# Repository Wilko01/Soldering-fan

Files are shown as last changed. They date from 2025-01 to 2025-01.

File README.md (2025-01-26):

# Soldering fume extractor

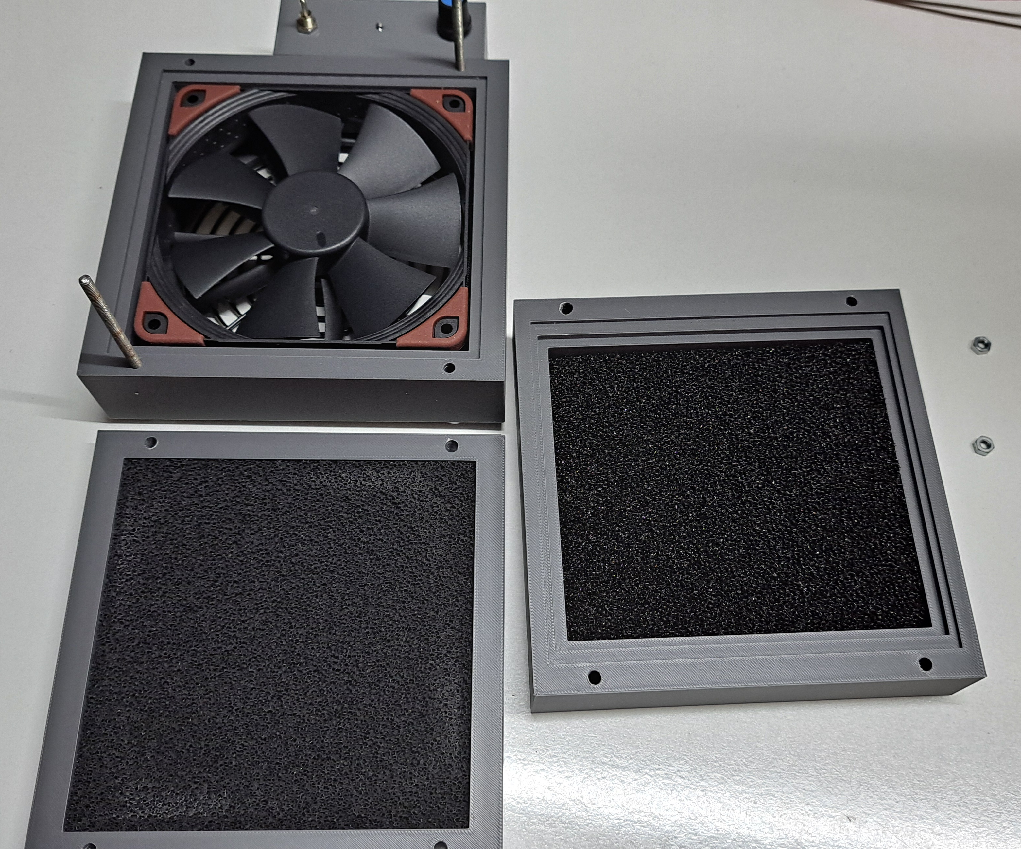
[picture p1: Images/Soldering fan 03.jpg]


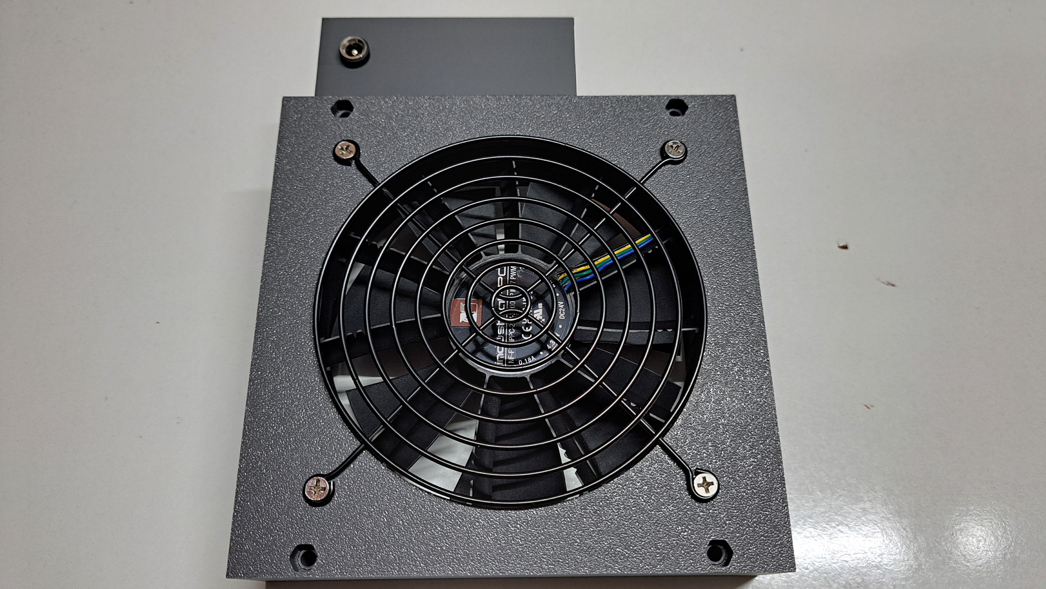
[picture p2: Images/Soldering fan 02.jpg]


## Description and operation instructions
Fumes which might be hazzourdus may be released during soldering. I therefor created a modular fume suction box. It can be used with active carbon, Hepa or any other filters.
The fan can be controlled via a potentiometer. Use a 24V, 2A power adapter. Turn the fan on via the switch. A green LED will turn on.

 ## Technical description
A 120mm 24V PC fan is used where the RPM is controlled via the PWM signal. A 555 generates the PWM signal. The PWM signal may not exceed 5V as it will damage the fan. The tacho of the fan is not used.
A more filters to the box, but keep in mind that by every filter the suction of the air will be reduced. The 555 will generate a 1kHz signal. This is not optimal as Noctua describes to use a 25kHz signal, but works fine.

PWM info: https://circuitdigest.com/fullimage?i=circuitdiagram/PWM-generation-using-555-timer-IC-circuit-diagram.png

### Parts
1 x Noctua NF-F12 industrialPPC-24V-3000 SP IP67
PLA filament
3 x 2-12mm screw
2 x 2,6-8mmm srew
4 x 85mm M4 bolt
4 x M4 cnut
Some wires

1 x 24V PWM fan

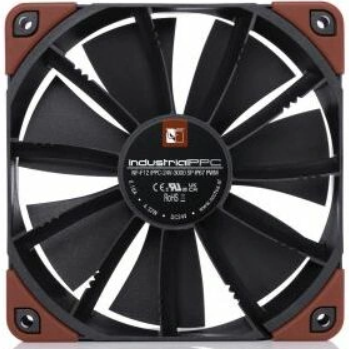
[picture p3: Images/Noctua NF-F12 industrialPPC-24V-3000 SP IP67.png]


1 x 555

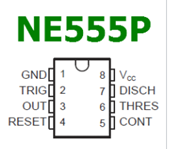
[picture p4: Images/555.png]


2 x 1N4148 Diode

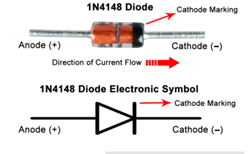
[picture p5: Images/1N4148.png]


1 x 5,5 x 2,1 mm DC power plug

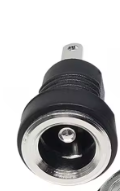
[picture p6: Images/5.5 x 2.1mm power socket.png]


1 x 10k Potentiometer
1 x 1k Resistor
1 x 100nF ceramic capacitor
1 x 7805 Voltage regulator
1 x switch
1 x 4k7 resistor
1 x 200k potentiometer
1 x 3mm green LED 

### Schematic overview
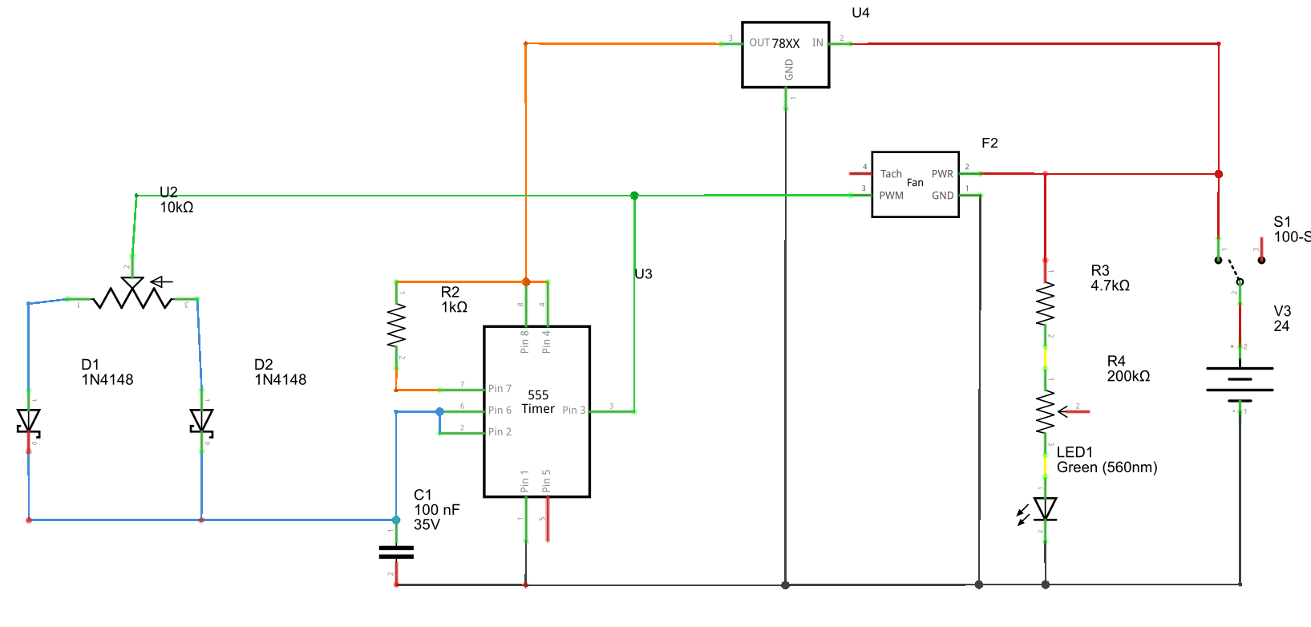
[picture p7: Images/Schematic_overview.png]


## 3D print parts
00 Soldering fan 01.3mf - contains all parts
Print in PLA and use support for the following prints
- Fan holder 05
- Electronics box

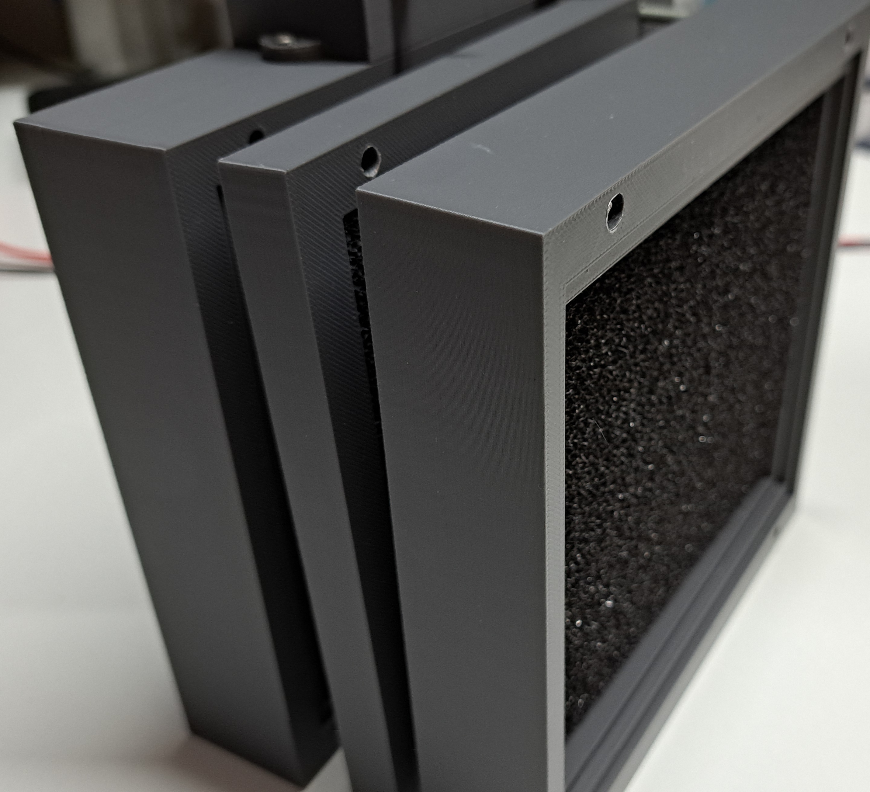
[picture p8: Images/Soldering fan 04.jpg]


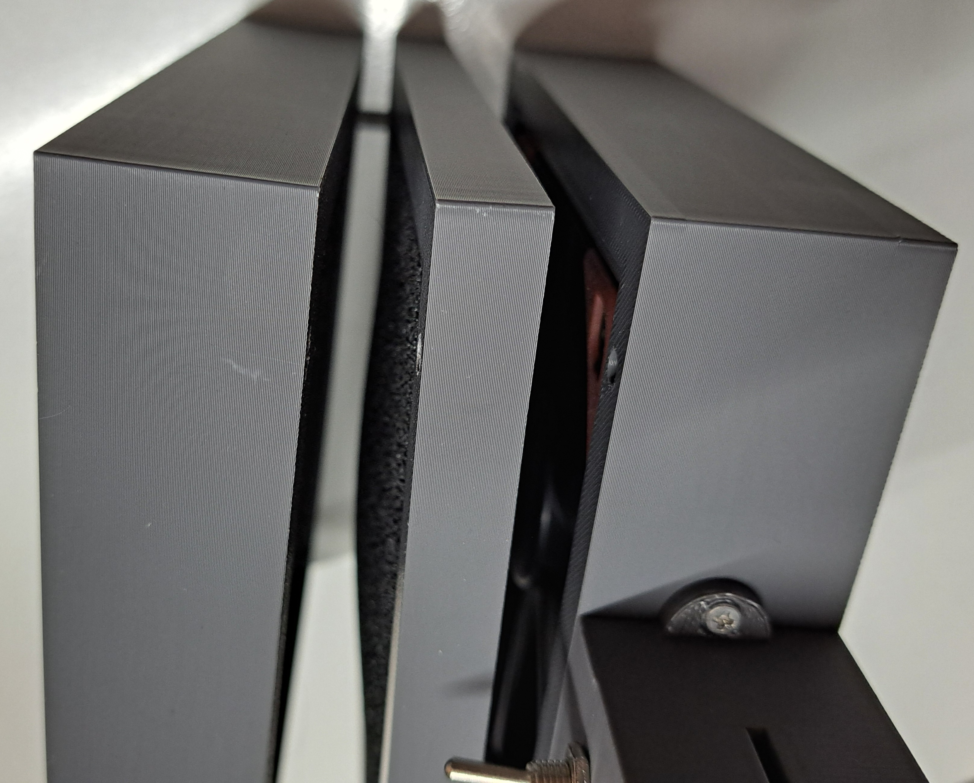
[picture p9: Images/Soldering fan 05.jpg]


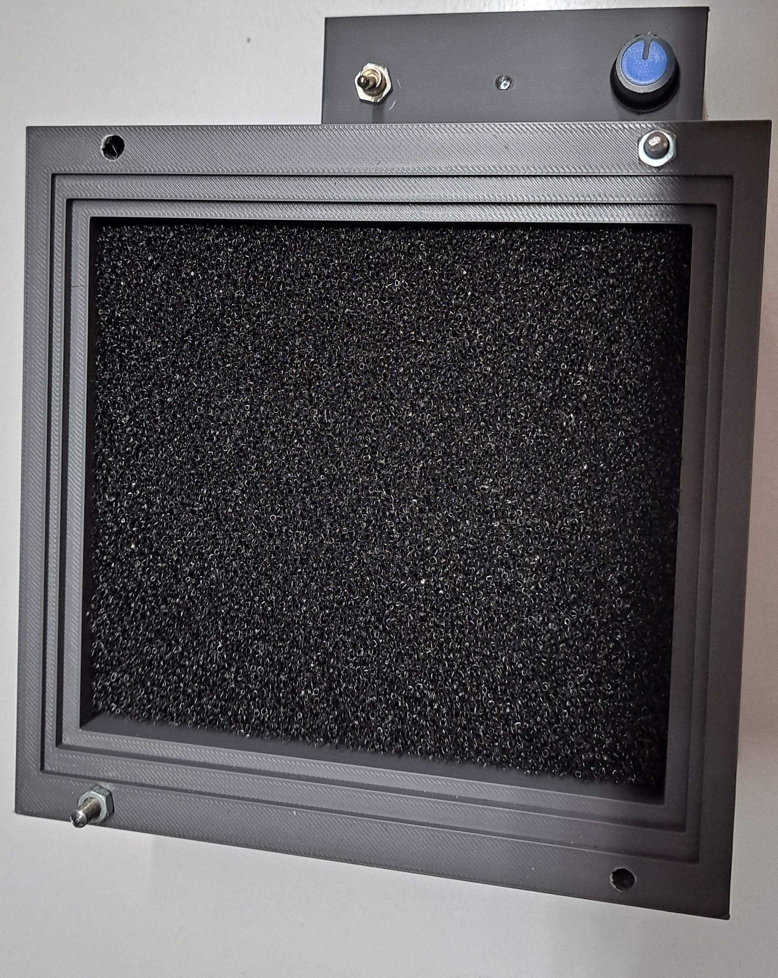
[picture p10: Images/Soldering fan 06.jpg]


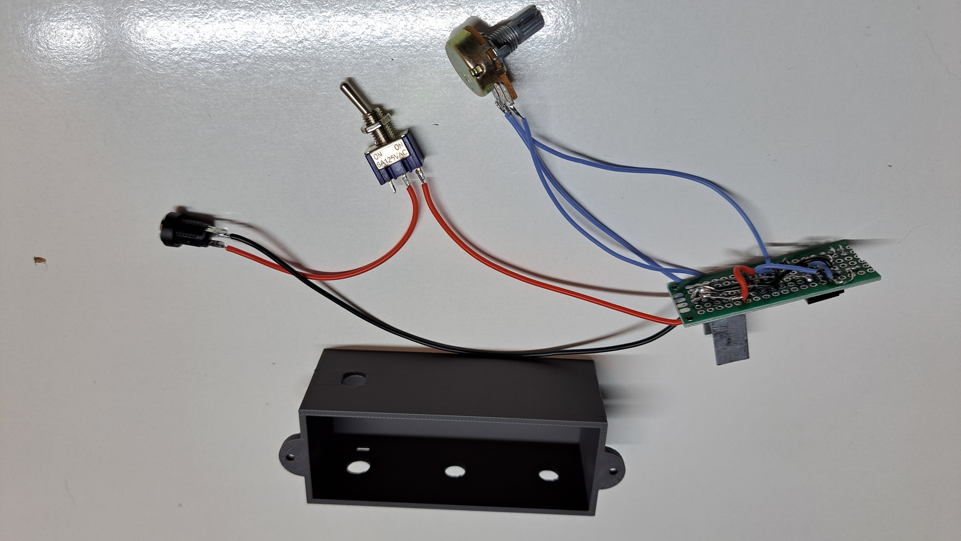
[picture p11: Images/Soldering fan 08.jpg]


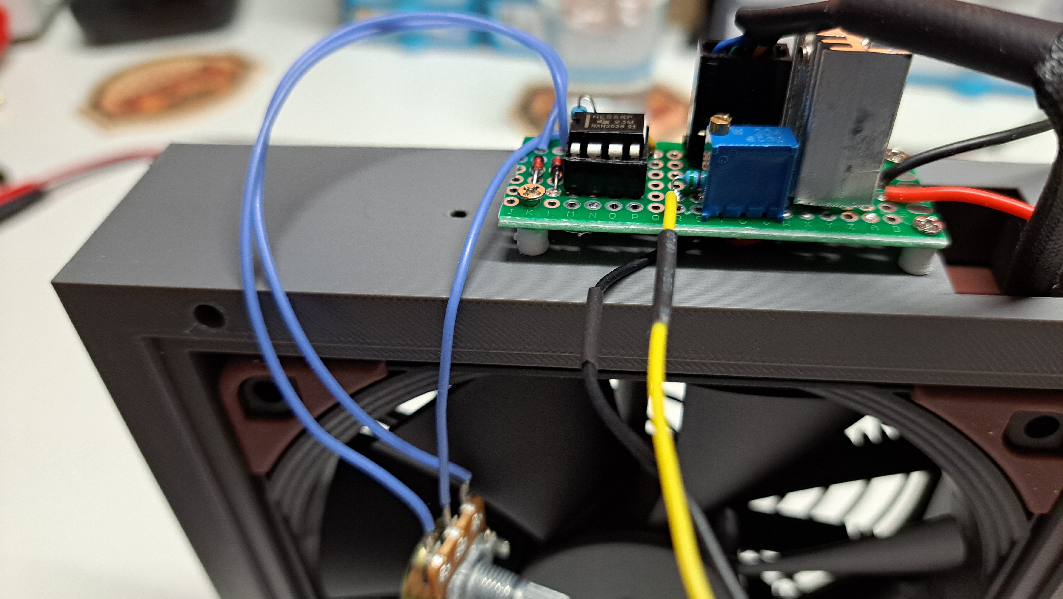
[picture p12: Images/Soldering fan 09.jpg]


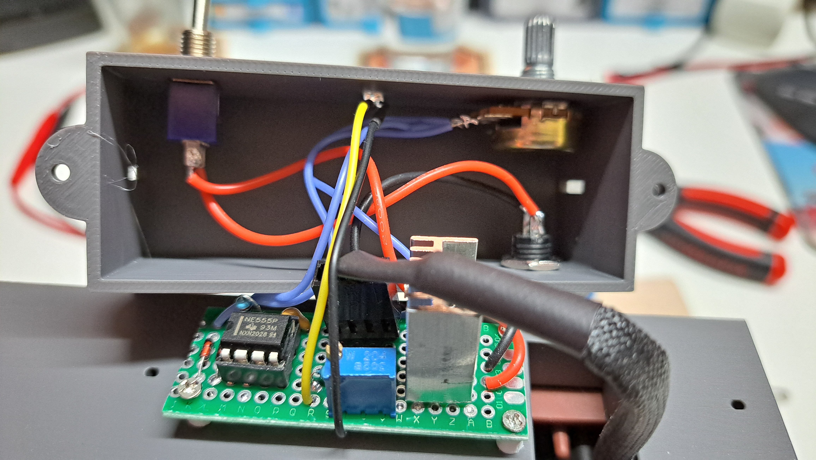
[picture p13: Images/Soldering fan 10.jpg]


### Mounting the fan
Guide the fan cable around the fan and position it into the 3D printed fan holder 

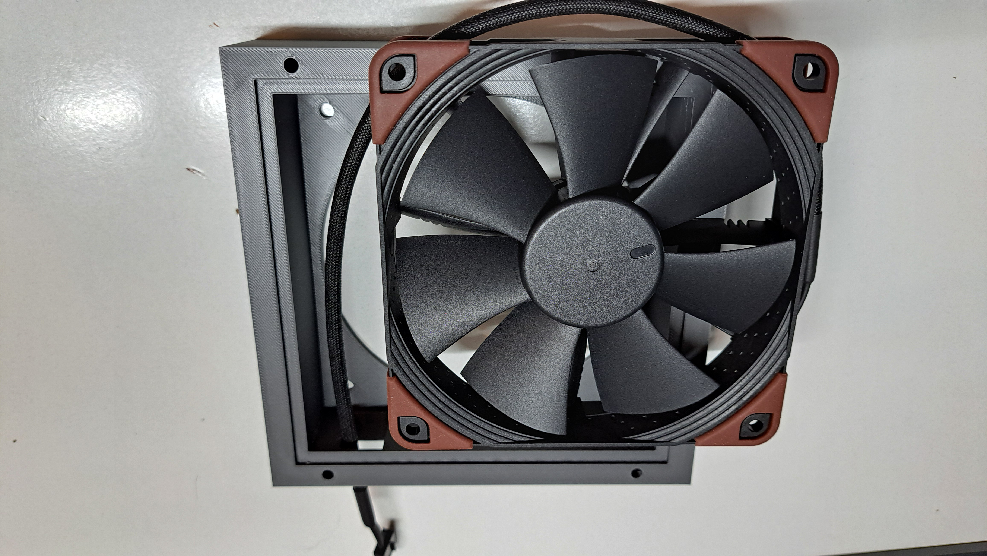
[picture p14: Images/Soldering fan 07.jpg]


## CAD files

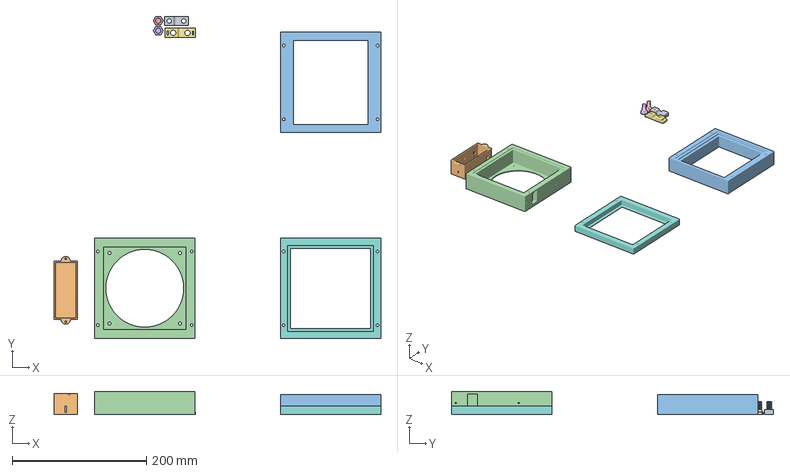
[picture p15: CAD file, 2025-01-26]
3D_Printer_Files/00 Soldering fan 01.3mf
487.7 x 480.8 x 35.0 mm
Bar clamp M8 L8 Tight 01.stl
Electronics box 05.stl
Hepa box 05.stl
Fan holder 05.stl
Bolt M8 L16 Tight 01.stl x 2
Bar clamp top 01.stl
Carbon box 05.stl

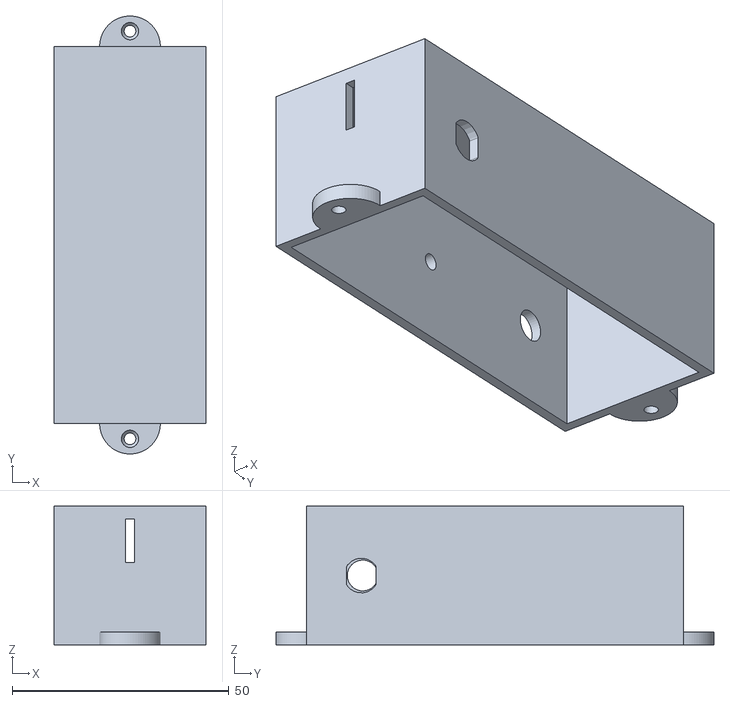
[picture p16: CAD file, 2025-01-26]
3D_Printer_Files/Electronics box 05.stl
35.0 x 101.0 x 32.0

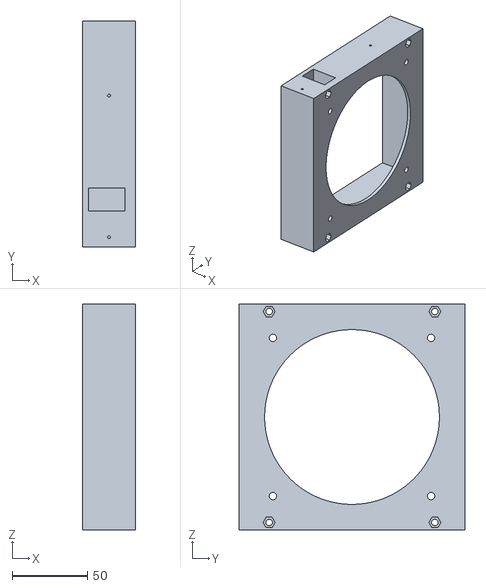
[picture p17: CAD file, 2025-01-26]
3D_Printer_Files/Fan holder 05.stl
35.0 x 150.0 x 150.0

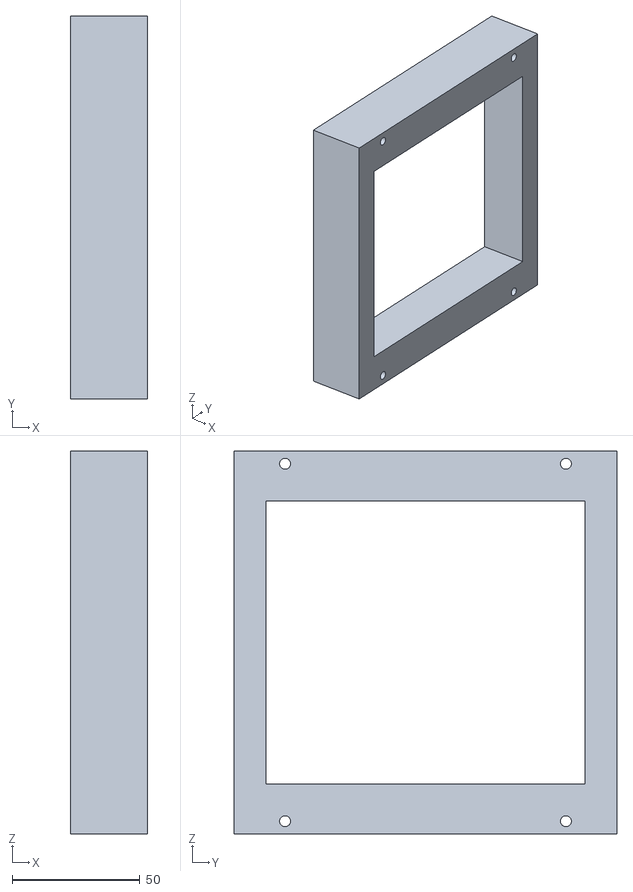
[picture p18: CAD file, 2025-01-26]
3D_Printer_Files/Hepa box 05.stl
30.1 x 150.0 x 150.0

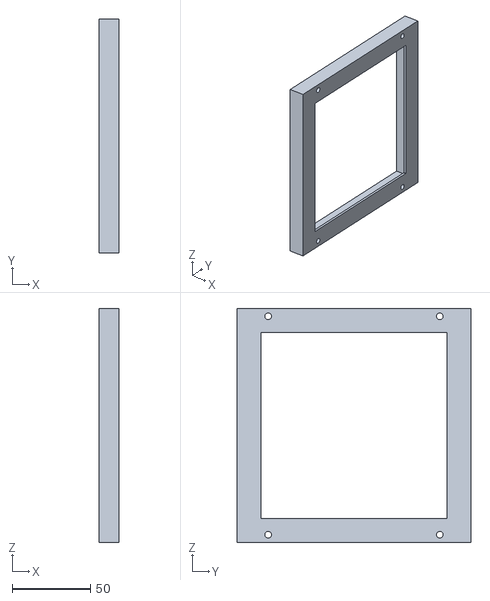
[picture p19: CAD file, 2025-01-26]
3D_Printer_Files/Carbon box 05.stl
13.0 x 150.0 x 150.0

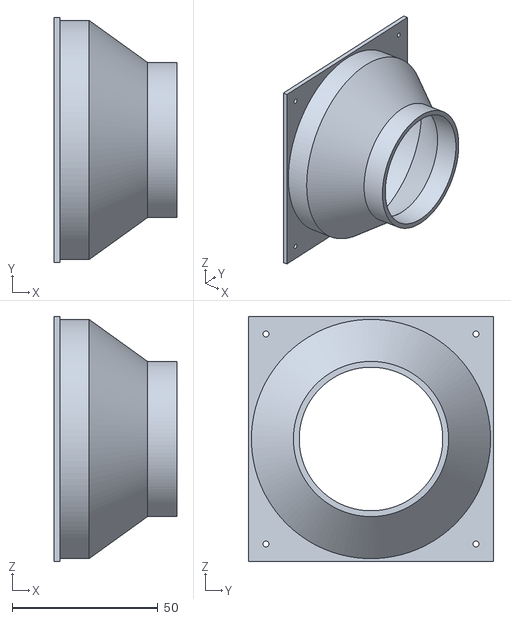
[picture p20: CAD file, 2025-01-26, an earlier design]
3D_Printer_Files/Old/Adaptor 02.stl
42.0 x 84.0 x 84.0

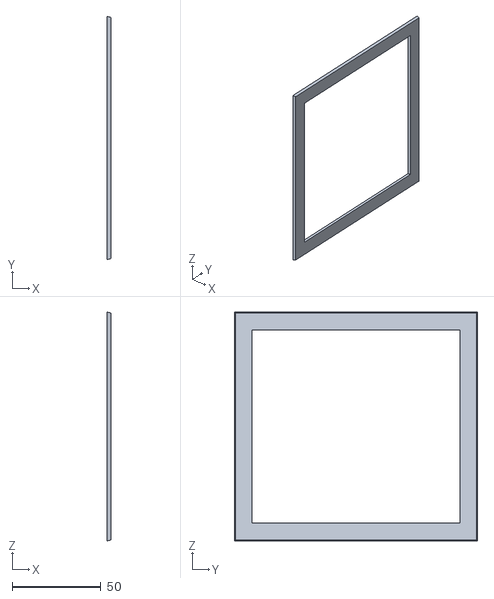
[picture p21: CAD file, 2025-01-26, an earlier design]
3D_Printer_Files/Old/Hepa filter pusher 04.stl
2.00 x 137.0 x 129.0

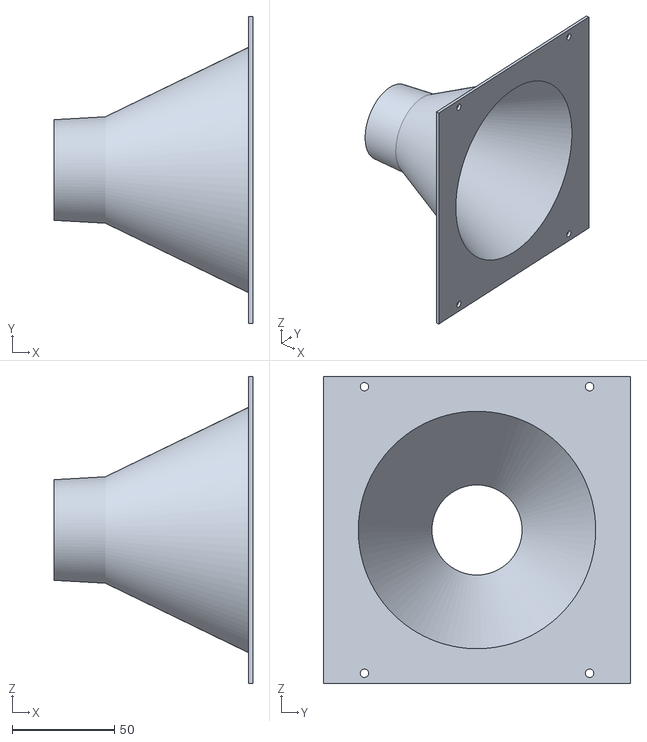
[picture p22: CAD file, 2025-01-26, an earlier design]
3D_Printer_Files/Old/Tube connector 01.stl
97.0 x 150.0 x 150.0

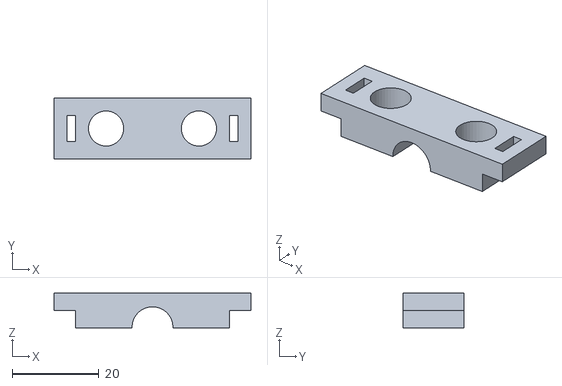
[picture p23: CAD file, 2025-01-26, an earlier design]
3D_Printer_Files/Old/Bar clamp top 01.stl
45.4 x 14.0 x 8.00

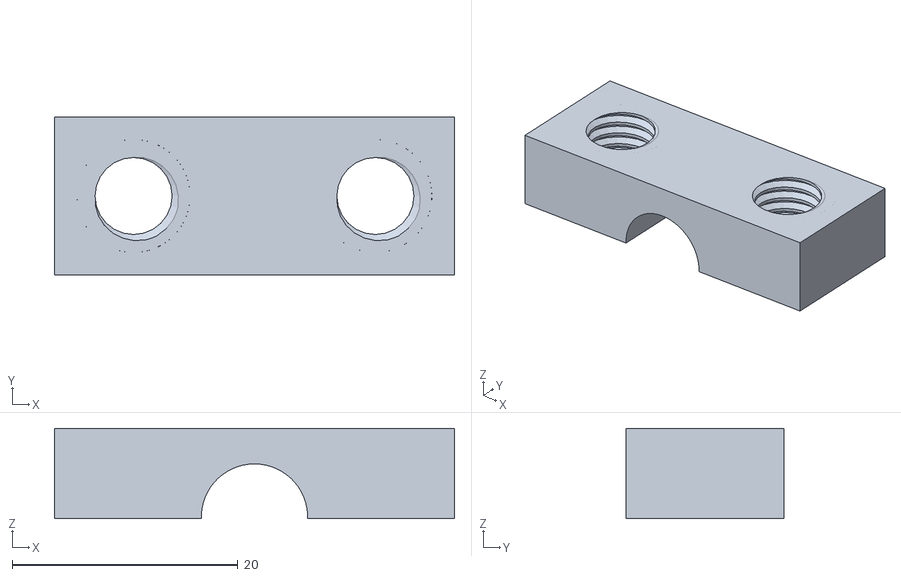
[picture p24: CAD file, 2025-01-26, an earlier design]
3D_Printer_Files/Old/Bar clamp M8 L8 Tight 01.stl
35.4 x 14.0 x 8.00

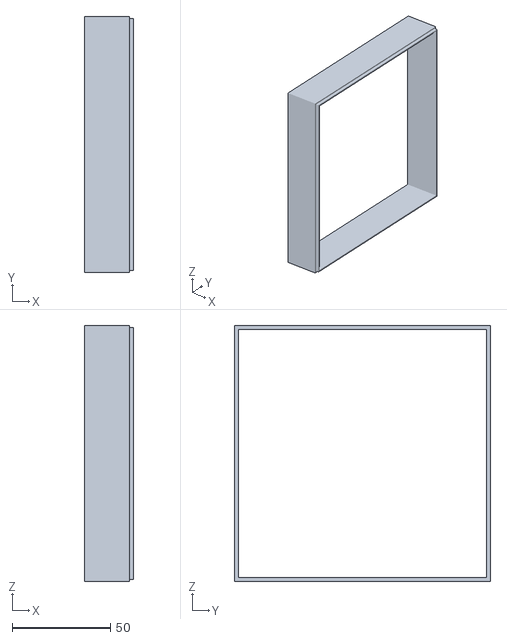
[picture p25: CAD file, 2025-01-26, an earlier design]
3D_Printer_Files/Old/Filter holder 23mm 01.stl
25.0 x 130.0 x 130.0

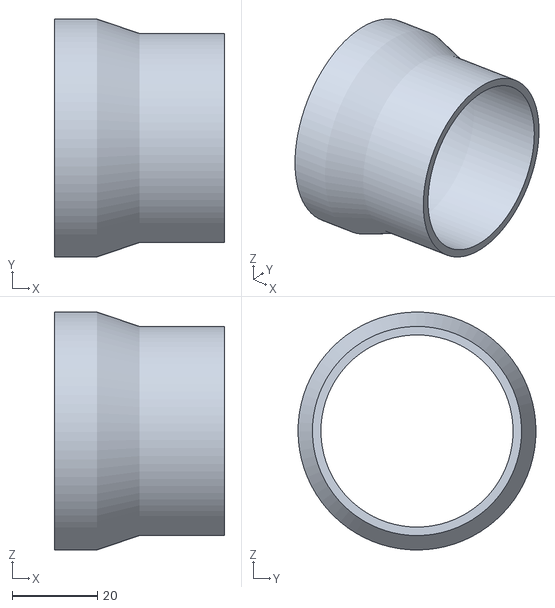
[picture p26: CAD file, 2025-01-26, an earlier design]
3D_Printer_Files/Old/Adaptor 24.6 - 26 01.stl
40.0 x 56.0 x 56.0

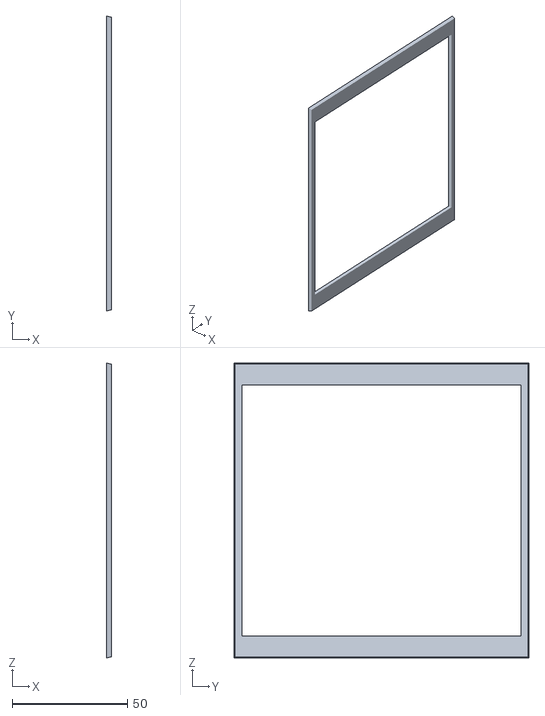
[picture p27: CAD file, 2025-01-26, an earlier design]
3D_Printer_Files/Old/Carbon filter pusher 03.stl
2.00 x 128.0 x 128.0

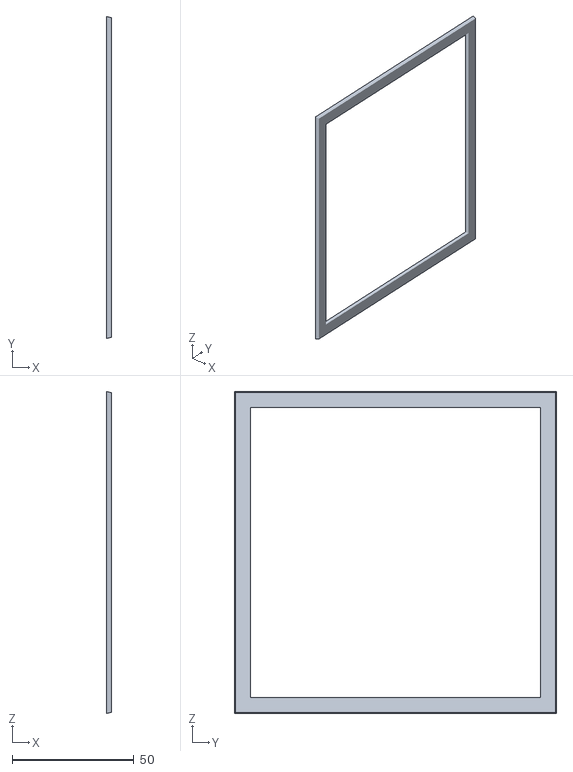
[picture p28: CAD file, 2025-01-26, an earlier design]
3D_Printer_Files/Old/Fan pusher 03.stl
2.00 x 132.0 x 132.0

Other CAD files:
3D_Printer_Files/Old/Tube connector 02.stl
3D_Printer_Files/Old/Bolt M8 L16 Tight 01.stl
3D_Printer_Files/Old/Soldering fan 01.skp
3D_Printer_Files/Old/Soldering fan 02.skp
3D_Printer_Files/Old/Soldering fan 03.skp
3D_Printer_Files/Old/Soldering fan 04.skp
3D_Printer_Files/Soldering fan 05.skp

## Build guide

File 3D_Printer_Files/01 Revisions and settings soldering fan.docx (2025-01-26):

# Print settings:

- Print material: PLA
- Rotation of the objects: No comment.
- Support: No
- Skirt, brim: Skirt.
- Bambu lab print profile: 0.2mm Strength profile

# Additional instructions

- None

# Materials needed

- PLA
- 4 x Bolt M4 x 85 or 90mm
- 4 x Lock nuts M4

# Log history

# Version 0.5

Fan holder 05

- Enlarged the gap of the 4mm bolt to 2.15 straal
- Adjusted the mounting positions for the electronic box
- Enlarged the gap for the fan so the cable can be winded around the fan and doesn’t need to be cut

Electronics box 05

- New design for the new electronics with 555 IC

Carbon box 05.stl

- Enlarged the gap of the 4mm bolt to 2.15 straal

Hepa box 05.stl

- Enlarged the gap of the 4mm bolt to 2.15 straal
- Shortened the gap for the HEPA filter by 2.2mm

# Version 0.4

Fan holder 04

- Enlarged the screws for the metal fan cover at the back from 2.3 to 2.45mm
- Enlarged the gap for the fan wire to pass thru
- Enlarged the gap for the fan to fit in by 0.1mm at each side
- Enlarged the gap of the 4mm bolt to 2.1 straal

Electronics box 04

- Increased the height and the width to fit the parts
- Added gap for potentiometer rotation fix

Carbon box 04.stl

- Enlarged the gap of the 4mm bolt to 2.1 straal

Hepa box 04.stl

- Enlarged the gap of the 4mm bolt to 2.1 straal

# Version 0.3

- Remove the parts that were extending into the previous part for simpler printing
- Added infill parts to push the previous part into position

# Version 0.2

- Ready to be printed with the parts extending into the previous part

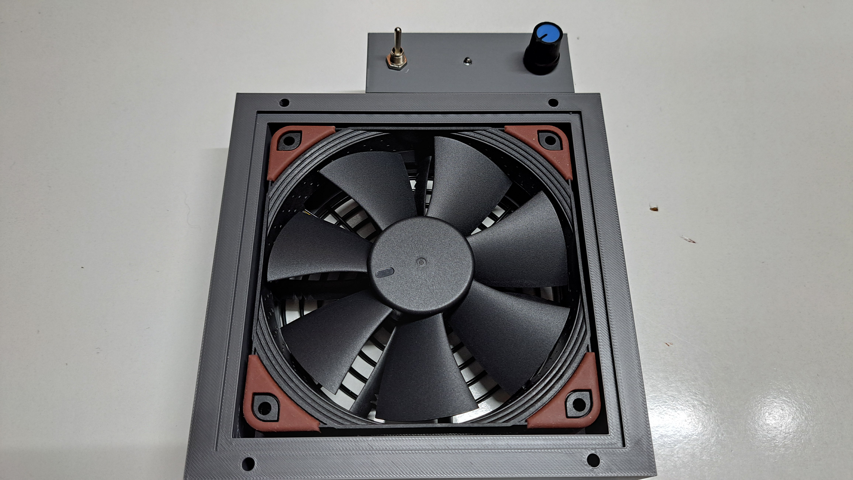
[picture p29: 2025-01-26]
Images/Soldering fan 01.jpg
